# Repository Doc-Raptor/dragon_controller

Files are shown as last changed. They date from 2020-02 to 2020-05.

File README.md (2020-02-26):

This is a controller-board for 3d printers from china which are based on the anet printers and using an 8-bit board with 
on-board stepper driver and sometimes no fuse-protection (and no thermal-run-away).
This board is a low cost replacement with an stm32f103ret and socketed stepper drivers.
It is also capable of runnung from 24v.

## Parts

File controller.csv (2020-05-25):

ID | Bezeichner | Gehäuse | Stückzahl | Bezeichnung | Anbieter und Referenz
1 | J10 | PhoenixContact_GMSTBVA_2,5_2-G-7,62_1x02_P7.62mm_Vertical | 1 | Power_Heat
2 | J3 | PhoenixContact_GMSTBVA_2,5_2-G-7,62_1x02_P7.62mm_Vertical | 1 | Power_IN
3 | J1 | PinHeader_1x03_P2.54mm_Vertical | 1 | SPI
4 | U2 | LQFP-64_10x10mm_P0.5mm | 1 | STM32F103RETx
5 | Y1 | Crystal_SMD_5032-2Pin_5.0x3.2mm | 1 | Crystal
6 | R22,R21,R18,R12 | R_1206_3216Metric | 4 | 4K7
7 | R17,R11 | R_1206_3216Metric | 2 | 100
8 | R3,R7 | R_1206_3216Metric | 2 | 10K
9 | R2 | R_1206_3216Metric | 1 | 1K
10 | Q3 | TO-263-3_TabPin2 | 1 | HUF76639S3ST
11 | Q2 | SOT-23 | 1 | PMV40UN2
12 | Q1 | TO-263-3_TabPin2 | 1 | HY4903B
13 | J60 | PinHeader_1x04_P2.54mm_Vertical | 1 | e0-Stepper
14 | J52 | PinHeader_2x03_P2.54mm_Vertical | 1 | J_Y
15 | J51 | PinHeader_2x03_P2.54mm_Vertical | 1 | J_X
16 | J50 | PinHeader_2x03_P2.54mm_Vertical | 1 | J_E0
17 | J49 | PinHeader_2x03_P2.54mm_Vertical | 1 | J_Z
18 | J46 | PinHeader_1x02_P2.54mm_Vertical | 1 | 3.3V
19 | J45 | PinHeader_1x02_P2.54mm_Vertical | 1 | 5V
20 | J44,J9 | PinHeader_1x04_P2.54mm_Vertical | 2 | z-Stepper
21 | J43 | PinHeader_1x02_P2.54mm_Vertical | 1 | VCC
22 | J39 | PinHeader_1x04_P2.54mm_Vertical | 1 | y-Stepper
23 | J33 | PinHeader_1x04_P2.54mm_Vertical | 1 | x-Stepper
24 | J31 | PinHeader_1x04_P2.54mm_Vertical | 1 | Serial
25 | J30 | PinHeader_2x05_P2.54mm_Vertical | 1 | EXP2
26 | J29 | PinHeader_2x05_P2.54mm_Vertical | 1 | EXP1
27 | J28 | PinHeader_1x07_P2.54mm_Vertical | 1 | SD_CARD
28 | J17 | PinHeader_1x03_P2.54mm_Vertical | 1 | X-
29 | J16 | PinHeader_1x03_P2.54mm_Vertical | 1 | MAX_END
30 | J15 | PinHeader_1x03_P2.54mm_Vertical | 1 | Y-
31 | J14 | PinHeader_1x03_P2.54mm_Vertical | 1 | EXP3
32 | J13 | PinHeader_1x03_P2.54mm_Vertical | 1 | Z-
33 | J12 | PinHeader_1x03_P2.54mm_Vertical | 1 | BOOT
34 | J8 | PinHeader_1x02_P2.54mm_Vertical | 1 | Fan_Cooler
35 | J7 | PinHeader_1x03_P2.54mm_Vertical | 1 | SV1
36 | J6 | PinHeader_1x03_P2.54mm_Vertical | 1 | TH_B
37 | J5 | PhoenixContact_MCV_1,5_2-G-5.08_1x02_P5.08mm_Vertical | 1 | Hotend
38 | J2 | PinHeader_1x03_P2.54mm_Vertical | 1 | TH_E
39 | F2 | Fuseholder_Blade_ATO_Littelfuse_Pudenz_2_Pin | 1 | F_Heatbed_15A
40 | F1 | Fuseholder_Blade_ATO_Littelfuse_Pudenz_2_Pin | 1 | Fuse_Power
41 | D11,D8,D2 | D_SOD-123 | 3 | 1N5819
42 | C26,C24,C22,C20 | CP_Elec_6.3x7.7 | 4 | 100uF
43 | C18,C13,C10,C9,C8,C7,C6,C1 | C_1206_3216Metric | 8 | 100nF
44 | C17,C14 | C_0603_1608Metric | 2 | 20pF
45 | C16,C15,C11,C19 | C_1206_3216Metric | 4 | 10uF
46 | C12,C3,C4 | C_0805_2012Metric | 3 | 1uF
47 | A4,A3,A2,A1 | Pololu_Breakout-16_15.2x20.3mm | 4 | Pololu_Breakout_A4988
48 | H1,H2,H3,H4 | MountingHole_3.2mm_M3 | 4 | MountingHole
49 | SW1 | SW_Push_SPST_NO_Alps_SKRK | 1 | SW_Push
50 | C2 | C_1206_3216Metric | 1 | 4.7uF
51 | C5 | C_0603_1608Metric | 1 | 33pF
52 | D1 | D_SMA | 1 | B140-13-F
53 | L1 | L_1812_4532Metric | 1 | 4.7uH
54 | R1 | R_1206_3216Metric | 1 | 124K
55 | R4 | R_1206_3216Metric | 1 | 23K7
56 | U1 | SOT-23-6 | 1 | MP2451
57 | U3 | SOT-23-5 | 1 | RT9013-33GB
58 | R5 | R_1206_3216Metric | 1 | 100K

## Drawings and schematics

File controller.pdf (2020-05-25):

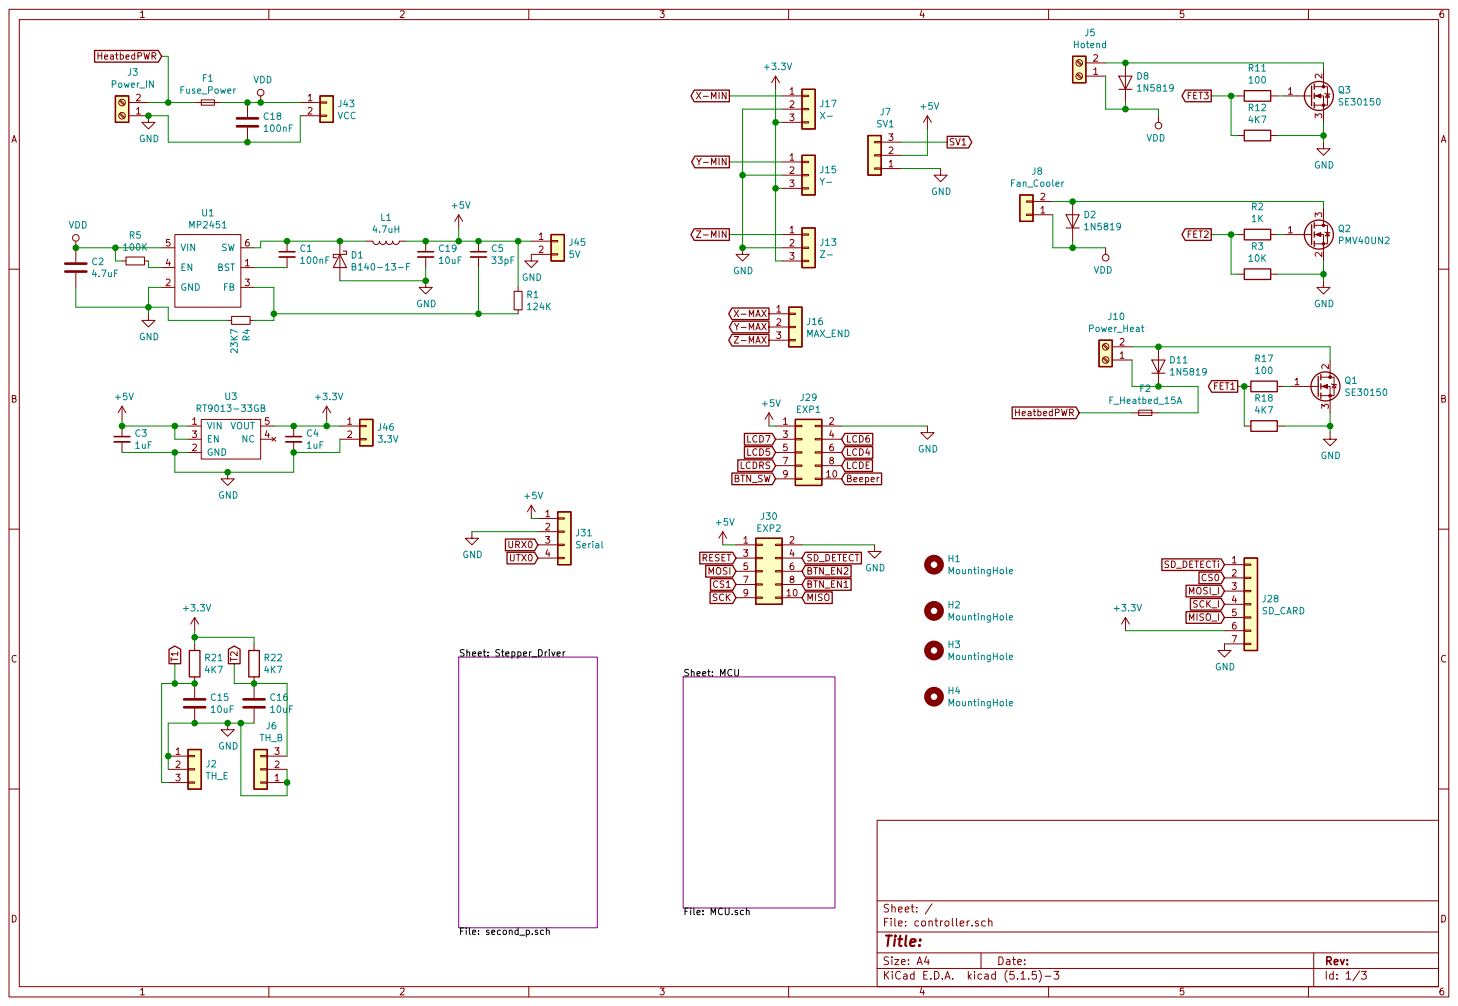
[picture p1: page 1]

Id: 1/3 Title: File: controller.sch Sheet: / Sheet: Stepper_Driver

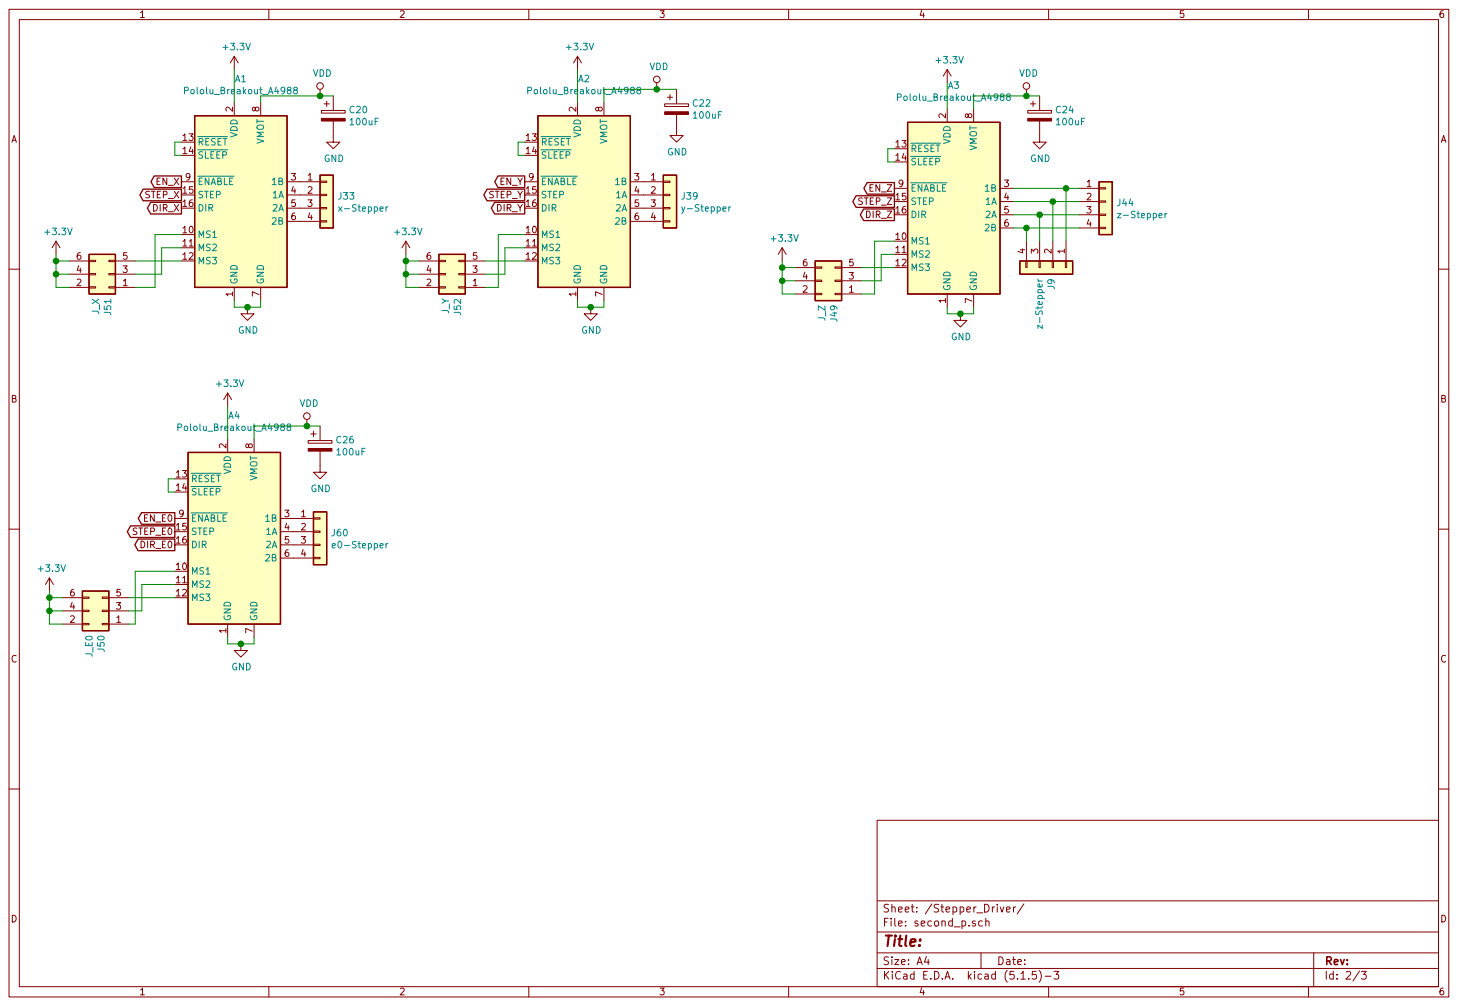
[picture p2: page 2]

8 ENABLE 9 A3 Pololu_Breakout_A4988 VDD GND GND GND

1 MS1 10 MS2 11 MS3 12 RESET 13 SLEEP 14 STEP 15 DIR 16 VDD

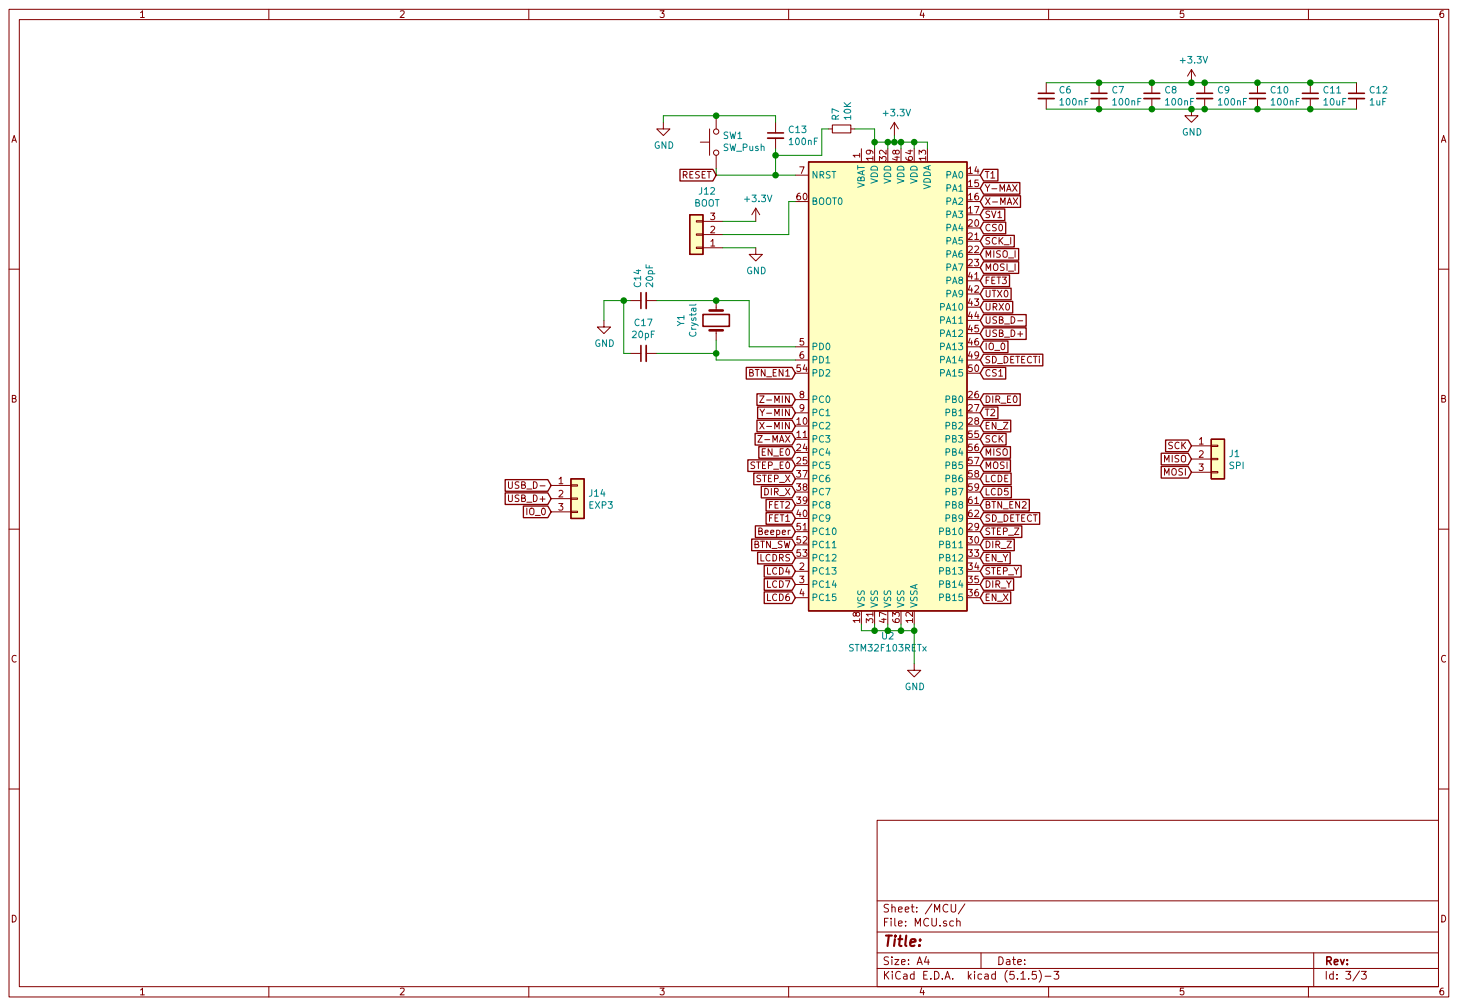
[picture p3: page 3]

Id: 3/3 Title: File: MCU.sch Sheet: /MCU/

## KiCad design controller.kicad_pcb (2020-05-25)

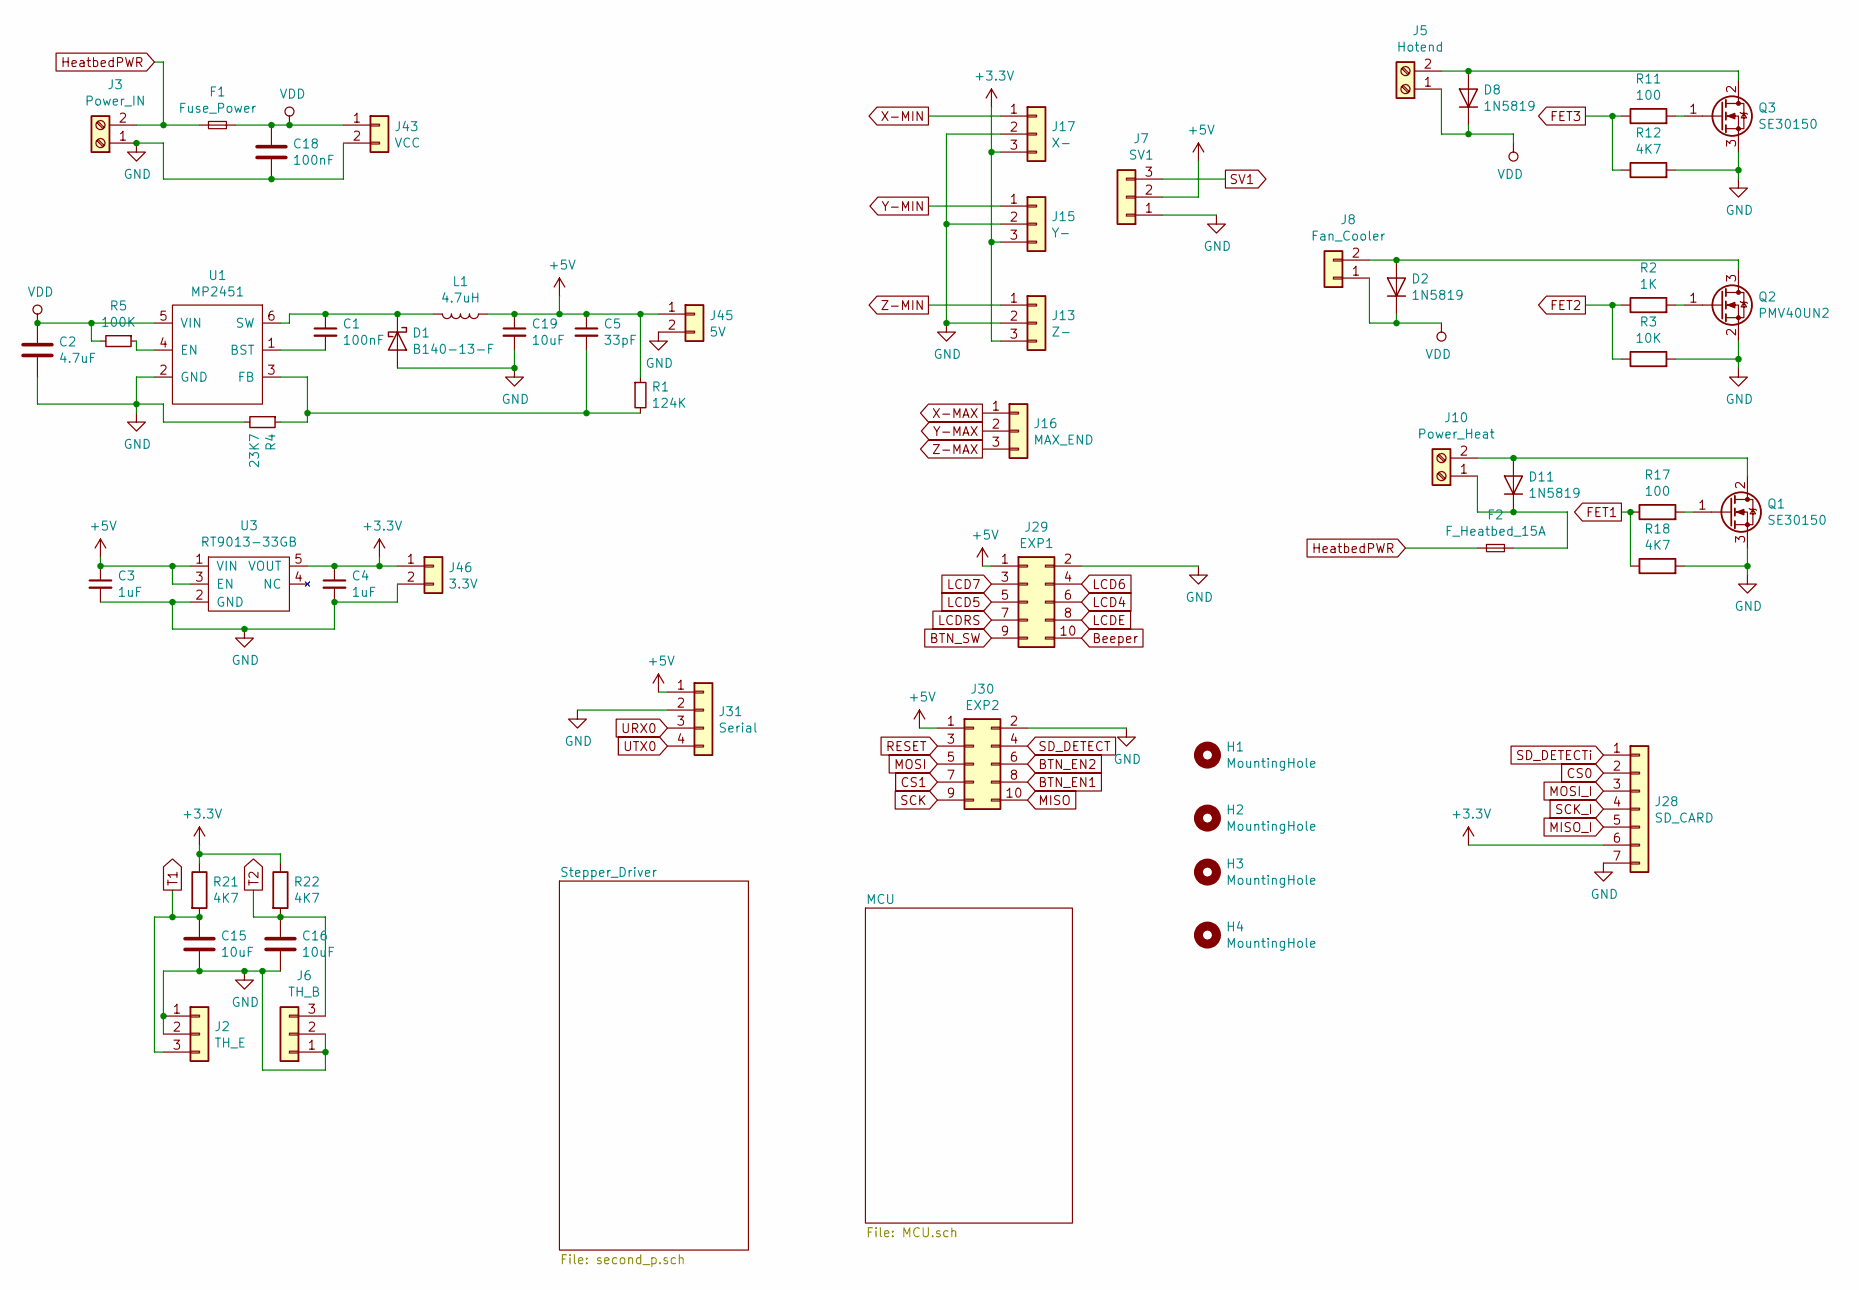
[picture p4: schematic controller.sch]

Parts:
C1, C18: 100nF; C_1206_3216Metric
C2: 4.7uF; C_1206_3216Metric
C3, C4: 1uF; C_0805_2012Metric
C5: 33pF; C_0603_1608Metric
C15, C16, C19: 10uF; C_1206_3216Metric
D1: B140-13-F; D_SMA
D2, D8, D11: 1N5819; D_SOD-123
F1: Fuse_Power; Fuseholder_Blade_ATO_Littelfuse_Pudenz_2_Pin
F2: F_Heatbed_15A; Fuseholder_Blade_ATO_Littelfuse_Pudenz_2_Pin
H1, H2, H3, H4: MountingHole; MountingHole_3.2mm_M3
J2: TH_E; PinHeader_1x03_P2.54mm_Vertical
J3: Power_IN; PhoenixContact_GMSTBVA_2,5_2-G-7,62_1x02_P7.62mm_Vertical
J5: Hotend; PhoenixContact_MCV_1,5_2-G-5.08_1x02_P5.08mm_Vertical
J6: TH_B; PinHeader_1x03_P2.54mm_Vertical
J7: SV1; PinHeader_1x03_P2.54mm_Vertical
J8: Fan_Cooler; PinHeader_1x02_P2.54mm_Vertical
J10: Power_Heat; PhoenixContact_GMSTBVA_2,5_2-G-7,62_1x02_P7.62mm_Vertical
J13: Z-; PinHeader_1x03_P2.54mm_Vertical
J15: Y-; PinHeader_1x03_P2.54mm_Vertical
J16: MAX_END; PinHeader_1x03_P2.54mm_Vertical
J17: X-; PinHeader_1x03_P2.54mm_Vertical
J28: SD_CARD; PinHeader_1x07_P2.54mm_Vertical
J29: EXP1; PinHeader_2x05_P2.54mm_Vertical
J30: EXP2; PinHeader_2x05_P2.54mm_Vertical
J31: Serial; PinHeader_1x04_P2.54mm_Vertical
J43: VCC; PinHeader_1x02_P2.54mm_Vertical
J45: 5V; PinHeader_1x02_P2.54mm_Vertical
J46: 3.3V; PinHeader_1x02_P2.54mm_Vertical
L1: 4.7uH; L_1812_4532Metric
Q1, Q3: SE30150; TO-263-3_TabPin2
Q2: PMV40UN2; SOT-23
R1: 124K; R_1206_3216Metric
R2: 1K; R_1206_3216Metric
R3: 10K; R_1206_3216Metric
R4: 23K7; R_1206_3216Metric
R5: 100K; R_1206_3216Metric
R11, R17: 100; R_1206_3216Metric
R12, R18, R21, R22: 4K7; R_1206_3216Metric
U1: MP2451; SOT-23-6
U3: RT9013-33GB; SOT-23-5

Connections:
+3V3: C4.1, J13.3, J15.3, J17.3, J28.6, J46.1, R21.1, R22.1, U3.5 (VOUT); also elsewhere on the board
+5V: C3.1, C5.1, C19.1, J7.2, J29.1, J30.1, J31.1, J45.1, L1.1, R1.1, U3.1 (VIN), U3.3 (EN)
BTN_EN1: J30.8; also elsewhere on the board
BTN_EN2: J30.6; also elsewhere on the board
BTN_SW: J29.9; also elsewhere on the board
Beeper: J29.10; also elsewhere on the board
CS0: J28.2; also elsewhere on the board
CS1: J30.7; also elsewhere on the board
FET1: R17.1, R18.1; also elsewhere on the board
FET2: R2.1, R3.1; also elsewhere on the board
FET3: R11.1, R12.1; also elsewhere on the board
GND: C2.2, C3.2, C4.2, C15.2, C16.2, C18.2, C19.2, D1.2 (A), J2.1, J2.2, J3.1, J6.1, J6.2, J7.1, J13.2, J15.2, J17.2, J28.7, J29.2, J30.2, J31.2, J43.2, J45.2, J46.2, Q1.3 (S), Q2.2 (S), Q3.3 (S), R3.2, R4.2, R12.2, R18.2, U1.2 (GND), U3.2 (GND); also elsewhere on the board
HeatbedPWR: F1.1, F2.1, J3.2
LCD4: J29.6; also elsewhere on the board
LCD5: J29.5; also elsewhere on the board
LCD6: J29.4; also elsewhere on the board
LCD7: J29.3; also elsewhere on the board
LCDE: J29.8; also elsewhere on the board
LCDRS: J29.7; also elsewhere on the board
MISO: J30.10; also elsewhere on the board
MISO_I: J28.5; also elsewhere on the board
MOSI: J30.5; also elsewhere on the board
MOSI_I: J28.3; also elsewhere on the board
unnamed: C1.1, D1.1 (K), L1.2, U1.6 (SW)
unnamed: C1.2, U1.1 (BST)
unnamed: C5.2, R1.2, R4.1, U1.3 (FB)
unnamed: D2.2 (A), J8.2, Q2.3 (D)
unnamed: D8.2 (A), J5.2, Q3.2 (D)
unnamed: D11.1 (K), F2.2, J10.1
unnamed: D11.2 (A), J10.2, Q1.2 (D)
unnamed: Q1.1 (G), R17.2
unnamed: Q2.1 (G), R2.2
unnamed: Q3.1 (G), R11.2
unnamed: R5.1, U1.4 (EN)
RESET: J30.3; also elsewhere on the board
SCK: J30.9; also elsewhere on the board
SCK_I: J28.4; also elsewhere on the board
SD_DETECT: J30.4; also elsewhere on the board
SD_DETECTi: J28.1; also elsewhere on the board
SV1: J7.3; also elsewhere on the board
T1: C15.1, J2.3, R21.2; also elsewhere on the board
T2: C16.1, J6.3, R22.2; also elsewhere on the board
URX0: J31.3; also elsewhere on the board
UTX0: J31.4; also elsewhere on the board
VDD: C2.1, C18.1, D2.1 (K), D8.1 (K), F1.2, J5.1, J8.1, J43.1, R5.2, U1.5 (VIN); also elsewhere on the board
X-MAX: J16.1; also elsewhere on the board
X-MIN: J17.1; also elsewhere on the board
Y-MAX: J16.2; also elsewhere on the board
Y-MIN: J15.1; also elsewhere on the board
Z-MAX: J16.3; also elsewhere on the board
Z-MIN: J13.1; also elsewhere on the board

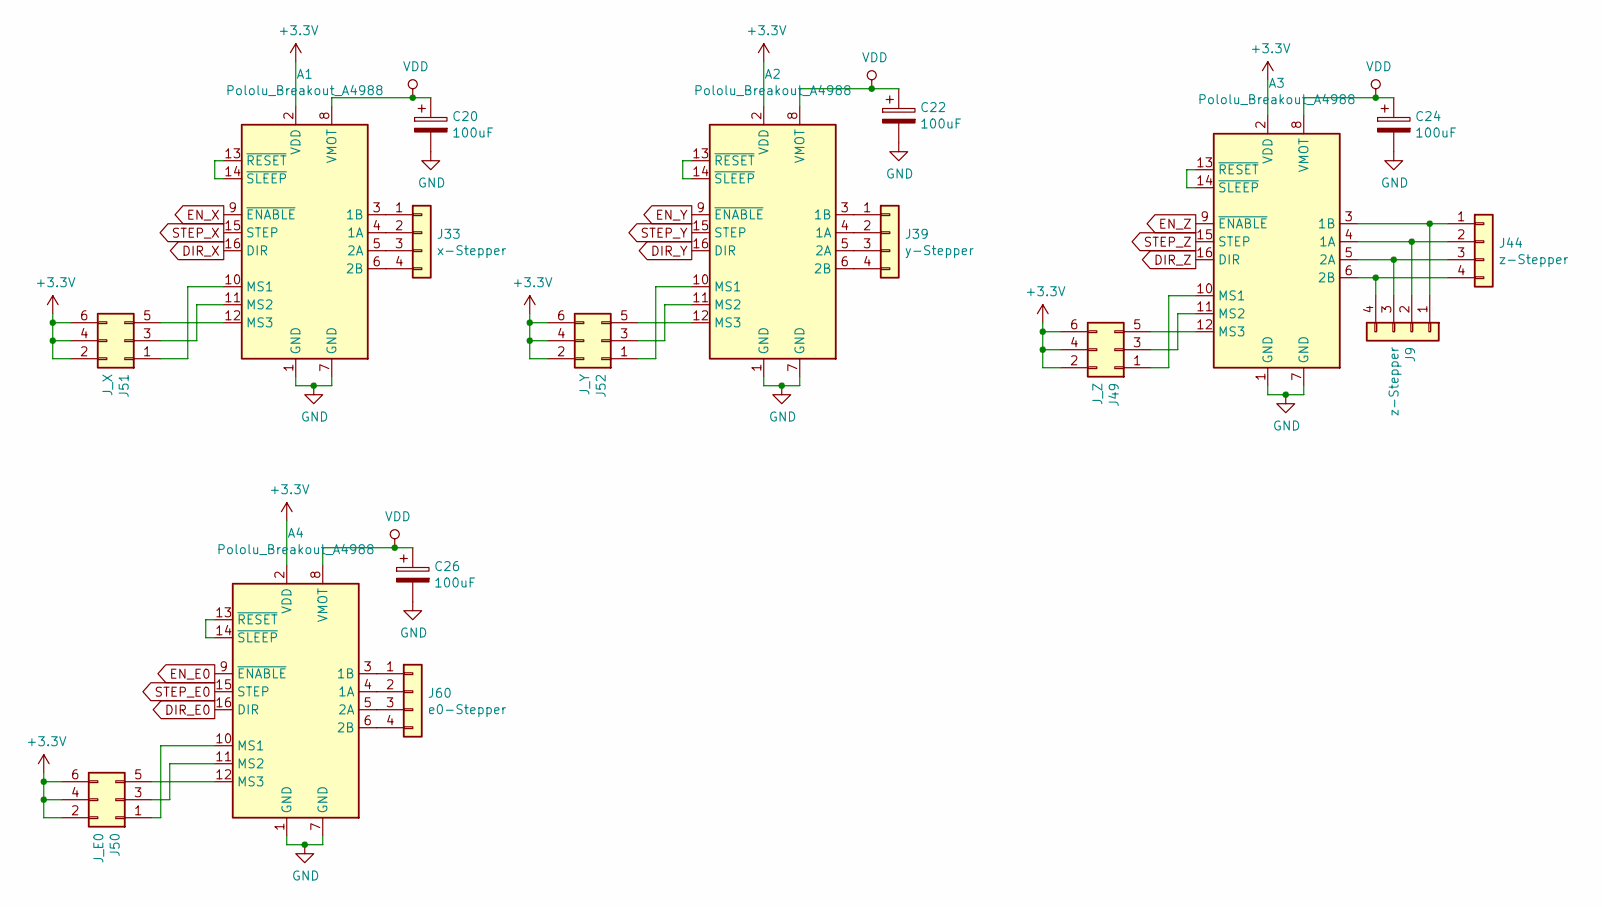
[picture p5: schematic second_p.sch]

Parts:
A1, A2, A3, A4: Pololu_Breakout_A4988; Pololu_Breakout-16_15.2x20.3mm
C20, C22, C24, C26: 100uF; CP_Elec_6.3x7.7
J9, J44: z-Stepper; PinHeader_1x04_P2.54mm_Vertical
J33: x-Stepper; PinHeader_1x04_P2.54mm_Vertical
J39: y-Stepper; PinHeader_1x04_P2.54mm_Vertical
J49: J_Z; PinHeader_2x03_P2.54mm_Vertical
J50: J_E0; PinHeader_2x03_P2.54mm_Vertical
J51: J_X; PinHeader_2x03_P2.54mm_Vertical
J52: J_Y; PinHeader_2x03_P2.54mm_Vertical
J60: e0-Stepper; PinHeader_1x04_P2.54mm_Vertical

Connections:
+3V3: A1.2 (VDD), A2.2 (VDD), A3.2 (VDD), A4.2 (VDD), J49.2, J49.4, J49.6, J50.2, J50.4, J50.6, J51.2, J51.4, J51.6, J52.2, J52.4, J52.6; also elsewhere on the board
DIR_E0: A4.16 (DIR); also elsewhere on the board
DIR_X: A1.16 (DIR); also elsewhere on the board
DIR_Y: A2.16 (DIR); also elsewhere on the board
DIR_Z: A3.16 (DIR); also elsewhere on the board
EN_E0: A4.9 (~ENABLE); also elsewhere on the board
EN_X: A1.9 (~ENABLE); also elsewhere on the board
EN_Y: A2.9 (~ENABLE); also elsewhere on the board
EN_Z: A3.9 (~ENABLE); also elsewhere on the board
GND: A1.1 (GND), A1.7 (GND), A2.1 (GND), A2.7 (GND), A3.1 (GND), A3.7 (GND), A4.1 (GND), A4.7 (GND), C20.2, C22.2, C24.2, C26.2; also elsewhere on the board
unnamed: A1.3 (1B), J33.1
unnamed: A1.4 (1A), J33.2
unnamed: A1.5 (2A), J33.3
unnamed: A1.6 (2B), J33.4
unnamed: A1.10 (MS1), J51.1
unnamed: A1.11 (MS2), J51.3
unnamed: A1.12 (MS3), J51.5
unnamed: A1.13 (~RESET), A1.14 (~SLEEP)
unnamed: A2.3 (1B), J39.1
unnamed: A2.4 (1A), J39.2
unnamed: A2.5 (2A), J39.3
unnamed: A2.6 (2B), J39.4
unnamed: A2.10 (MS1), J52.1
unnamed: A2.11 (MS2), J52.3
unnamed: A2.12 (MS3), J52.5
unnamed: A2.13 (~RESET), A2.14 (~SLEEP)
unnamed: A3.3 (1B), J9.1, J44.1
unnamed: A3.4 (1A), J9.2, J44.2
unnamed: A3.5 (2A), J9.3, J44.3
unnamed: A3.6 (2B), J9.4, J44.4
unnamed: A3.10 (MS1), J49.1
unnamed: A3.11 (MS2), J49.3
unnamed: A3.12 (MS3), J49.5
unnamed: A3.13 (~RESET), A3.14 (~SLEEP)
unnamed: A4.3 (1B), J60.1
unnamed: A4.4 (1A), J60.2
unnamed: A4.5 (2A), J60.3
unnamed: A4.6 (2B), J60.4
unnamed: A4.10 (MS1), J50.1
unnamed: A4.11 (MS2), J50.3
unnamed: A4.12 (MS3), J50.5
unnamed: A4.13 (~RESET), A4.14 (~SLEEP)
STEP_E0: A4.15 (STEP); also elsewhere on the board
STEP_X: A1.15 (STEP); also elsewhere on the board
STEP_Y: A2.15 (STEP); also elsewhere on the board
STEP_Z: A3.15 (STEP); also elsewhere on the board
VDD: A1.8 (VMOT), A2.8 (VMOT), A3.8 (VMOT), A4.8 (VMOT), C20.1, C22.1, C24.1, C26.1; also elsewhere on the board

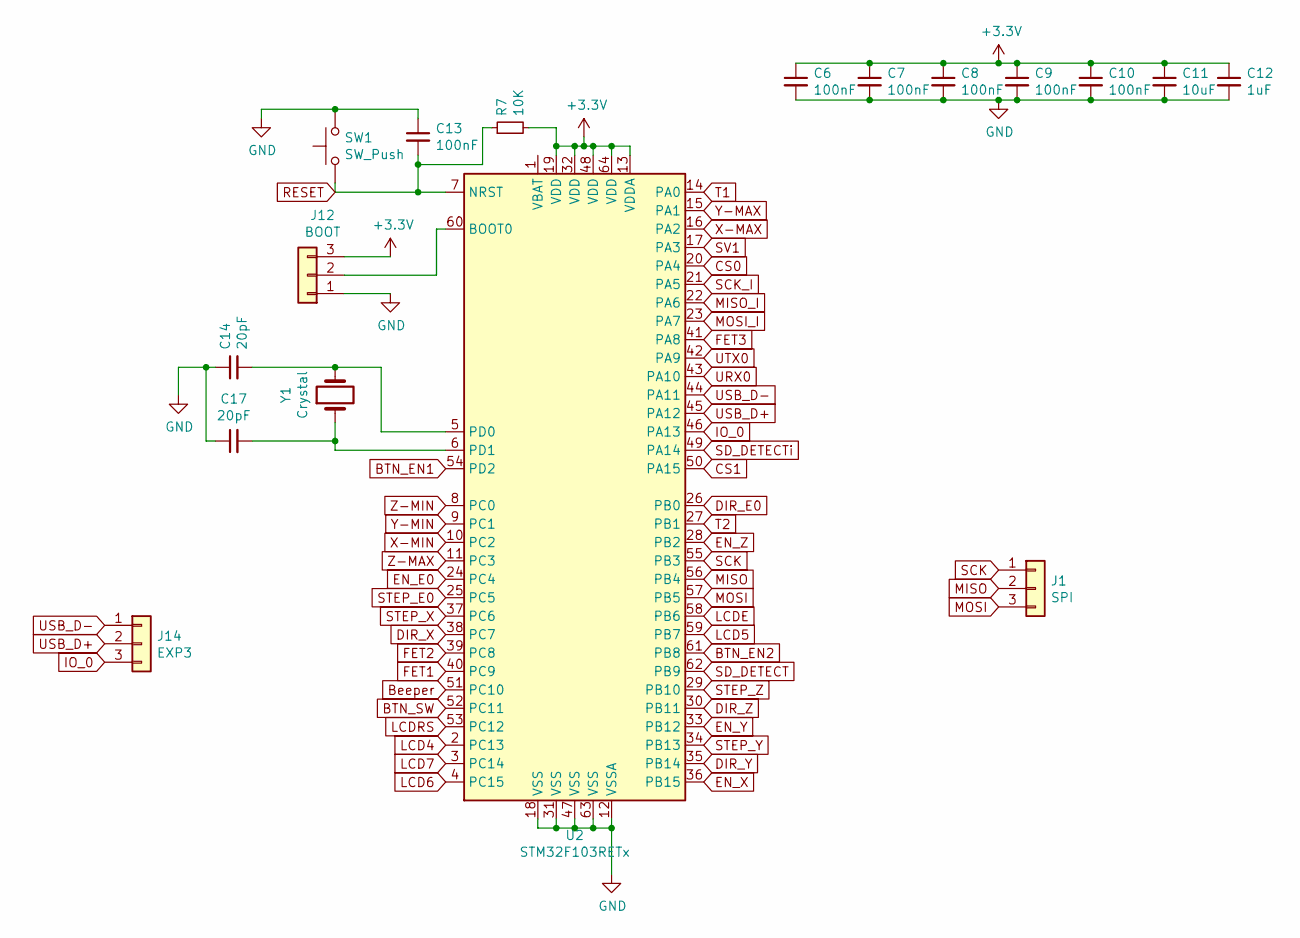
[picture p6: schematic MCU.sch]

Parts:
C6, C7, C8, C9, C10, C13: 100nF; C_1206_3216Metric
C11: 10uF; C_1206_3216Metric
C12: 1uF; C_0805_2012Metric
C14, C17: 20pF; C_0603_1608Metric
J1: SPI; PinHeader_1x03_P2.54mm_Vertical
J12: BOOT; PinHeader_1x03_P2.54mm_Vertical
J14: EXP3; PinHeader_1x03_P2.54mm_Vertical
R7: 10K; R_1206_3216Metric
SW1: SW_Push; SW_Push_SPST_NO_Alps_SKRK
U2: STM32F103RETx; LQFP-64_10x10mm_P0.5mm
Y1: Crystal; Crystal_SMD_5032-2Pin_5.0x3.2mm

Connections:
+3V3: C6.1, C7.1, C8.1, C9.1, C10.1, C11.1, C12.1, J12.3, R7.2, U2.13 (VDDA), U2.19 (VDD), U2.32 (VDD), U2.48 (VDD), U2.64 (VDD); also elsewhere on the board
BTN_EN1: U2.54 (PD2); also elsewhere on the board
BTN_EN2: U2.61 (PB8); also elsewhere on the board
BTN_SW: U2.52 (PC11); also elsewhere on the board
Beeper: U2.51 (PC10); also elsewhere on the board
CS0: U2.20 (PA4); also elsewhere on the board
CS1: U2.50 (PA15); also elsewhere on the board
DIR_E0: U2.26 (PB0); also elsewhere on the board
DIR_X: U2.38 (PC7); also elsewhere on the board
DIR_Y: U2.35 (PB14); also elsewhere on the board
DIR_Z: U2.30 (PB11); also elsewhere on the board
EN_E0: U2.24 (PC4); also elsewhere on the board
EN_X: U2.36 (PB15); also elsewhere on the board
EN_Y: U2.33 (PB12); also elsewhere on the board
EN_Z: U2.28 (PB2); also elsewhere on the board
FET1: U2.40 (PC9); also elsewhere on the board
FET2: U2.39 (PC8); also elsewhere on the board
FET3: U2.41 (PA8); also elsewhere on the board
GND: C6.2, C7.2, C8.2, C9.2, C10.2, C11.2, C12.2, C13.1, C14.1, C17.1, J12.1, SW1.2, U2.12 (VSSA), U2.18 (VSS), U2.31 (VSS), U2.47 (VSS), U2.63 (VSS); also elsewhere on the board
IO_0: J14.3, U2.46 (PA13)
LCD4: U2.2 (PC13); also elsewhere on the board
LCD5: U2.59 (PB7); also elsewhere on the board
LCD6: U2.4 (PC15); also elsewhere on the board
LCD7: U2.3 (PC14); also elsewhere on the board
LCDE: U2.58 (PB6); also elsewhere on the board
LCDRS: U2.53 (PC12); also elsewhere on the board
MISO: J1.2, U2.56 (PB4); also elsewhere on the board
MISO_I: U2.22 (PA6); also elsewhere on the board
MOSI: J1.3, U2.57 (PB5); also elsewhere on the board
MOSI_I: U2.23 (PA7); also elsewhere on the board
unnamed: C14.2, U2.5 (PD0), Y1.2
unnamed: C17.2, U2.6 (PD1), Y1.1
unnamed: J12.2, U2.60 (BOOT0)
RESET: C13.2, R7.1, SW1.1, U2.7 (NRST); also elsewhere on the board
SCK: J1.1, U2.55 (PB3); also elsewhere on the board
SCK_I: U2.21 (PA5); also elsewhere on the board
SD_DETECT: U2.62 (PB9); also elsewhere on the board
SD_DETECTi: U2.49 (PA14); also elsewhere on the board
STEP_E0: U2.25 (PC5); also elsewhere on the board
STEP_X: U2.37 (PC6); also elsewhere on the board
STEP_Y: U2.34 (PB13); also elsewhere on the board
STEP_Z: U2.29 (PB10); also elsewhere on the board
SV1: U2.17 (PA3); also elsewhere on the board
T1: U2.14 (PA0); also elsewhere on the board
T2: U2.27 (PB1); also elsewhere on the board
URX0: U2.43 (PA10); also elsewhere on the board
USB_D+: J14.2, U2.45 (PA12)
USB_D-: J14.1, U2.44 (PA11)
UTX0: U2.42 (PA9); also elsewhere on the board
X-MAX: U2.16 (PA2); also elsewhere on the board
X-MIN: U2.10 (PC2); also elsewhere on the board
Y-MAX: U2.15 (PA1); also elsewhere on the board
Y-MIN: U2.9 (PC1); also elsewhere on the board
Z-MAX: U2.11 (PC3); also elsewhere on the board
Z-MIN: U2.8 (PC0); also elsewhere on the board

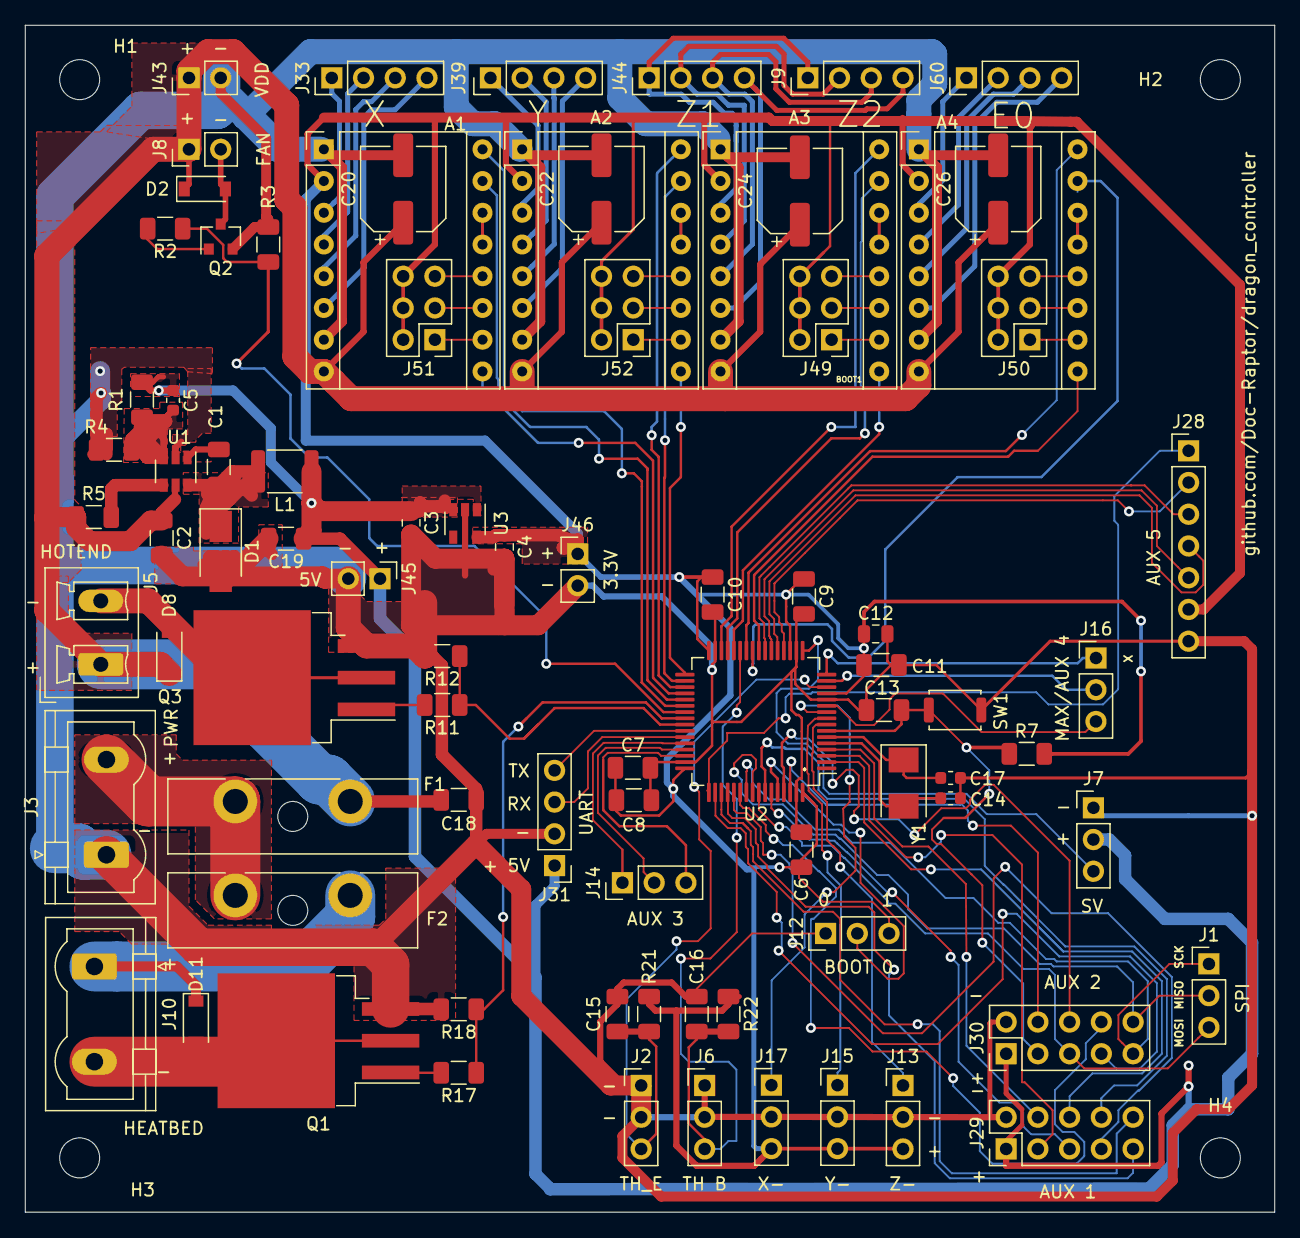
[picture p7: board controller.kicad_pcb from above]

Board: 2 copper layers, 100.0 x 95.0 mm, 88 parts (0 on the bottom side), 101 nets.

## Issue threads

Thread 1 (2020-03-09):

a bit of criticism.

r-pv, 2020-03-09:
Hi there, I'm thinking for a bit now to build an stm32 controller board too, so if you allow me to put my two cents on your board I think I can give you a little help.

So the first thing it's the mosfet you choose ( HUF76639S3ST ), didn't seems to be adequate for this task, their RDSON seems huge for the task, for the bed you should look for something below 10mΩ, the mosfet that you're using are 27mΩ at 10v, but you'll be using 3.3v for the gate so, if a read correctly the datasheet, you should be getting way higher RSDSON that the advertised 27mΩ and you'll get around 40mΩ, so if you are planing to use this at 24v on a typical 120w bed that'll be around 1W heat on the mosfet, you'll need active cooling (FAN)  and  for a 12v system that's 4W, I think this won't work for much. I'm planning to use the AON6522 or the AON7420, maybe a mix of both.

Next, the switching converter seems too old, you should look for a modern switching converter, after all, you won't be using more than 200mA for this. So for a 24v systems something like the MP1584 or the MP2451 are more than OK, for 12v you can use something like the MP2359.
In the same point, your layout for the switching converter are quite bad, on the datasheet of the IC that you'll be using check for the "layout recommendation" part and duplicate it, literately, big planes and component positions. If you are using a modern switching converter with a layout like you used on this controller it just won't work.

The tracks seems a bit thin, at least for the bed.

Cheers!.

Doc-Raptor, 2020-03-10:
Thanks for the Tips. I took the mosfet for the bed only for testing in the moment until I find something better. I only got the boards yesterday.
With the switching converter: It is not the newest and overkill, but literary every manufacturer has one in their lineup and it works even on a crued layout if it is under light load, but I will look in to the ones you recommended.
And I will increase the thickness of some of the tracks, when I finalize the layout and flood the pcb in some places with power and ground

Thanks and have a nice day

r-pv, 2020-03-11:
So I made a mistake, it's AON7520 (not 7420). If you like the THT mosfets the irlb8743 seems nice too, I'm using a controller with this mosfets and it's OK with 3v3 logic level. But if you can get a "gate driver" will be the best, but are a bit hard to get, at least to me.

Regarding the DC converter, you really should ditch it, not just because it's old, more because its working frequency, 52khz, it'll produce tons of EMI and probably will mess with the ADC readings if not with all, at very least you should add an RC filter after its output. The AMS1117, I used it and liked a lot but requires a lot of capacitance for working properly, I recently ditched it for the RT9013, all the new regulators are smaller, smarter, requires fewer capacitance/inductance and they just work better.

May I ask why you choose the F103RET MCU?, this part it's why I really decide anything, I what a simple controller without too much specs.

Cheers!.

Doc-Raptor, 2020-03-14:
I will be testing the HY4903B and SE30150. I bought them a few months ago most of them for someone else to safe shipping cost when I bought some PMV40UN2 and some other stuff. They have a RSDSON of 2mΩ when I looked it up two days ago. And they should drop in very easily.

The RT9013 sounds very good. When this board works I will replace the AMS1117 for the RT9013. Also the LM2575 could be replaced.

The F103RET (the f103 series in generaly) overing a lot for a relative low price. The F103RET should have enough memory for the firmware (if not the F103RF and F103RG should drop rigth in without problems). There are other factors, but overall the stm32f103 series overs for the price a lot.

r-pv, 2020-03-14:
The HY4903B sounds pretty good, at 3V3 seems that you'll get around 8mΩ, the SE30150 _seems_ better but the gate threshold it's at max 3v, too close to the 3V3 voltage, may not work, also, the datasheet didn't included an RDSOn graph to see how much resistance you can expect. Now, if you can get something that be a level shifter (PWM from 3v3 to 5v or 10v), that's another case!, ST has a [3printer board controller](https://www.st.com/en/evaluation-tools/steval-3dp001v1.html) that uses the SN74LVC1G125 as a level shifter, to get 5v PWM (or you can get a proper gate/mosfet driver). With an 5v PWM you will get an RDSOn of 2.1mΩ on the SE30150 and 3mΩ on the HY4903B.

The PMV40UN2 for switching FAN outputs seems pretty good, I'll use the AO34000A, but for this task there's not really any difference.

Cheers.

r-pv, 2020-03-18:
Hi, now it's looking great, just the layout requires a few details, check the datasheet of the IC: it says that you should put the components as close as possible (specially the capacitors), also, components like the mp2451 and modern switching regulators that work at high frequencies they need a big ground plane (you should use all available space on your pcb as ground plane, normally it's a good practice), I'll post how's the layout that I use and know that really works. The layout it's super important for this type of regulators, I remember that I used a layout like on your previous design for the MP1584, the regulator just give a random output from 50% to 95% of the VIN, it just won't work.

[rSTM32F103RCT6.pdf](https://github.com/Doc-Raptor/dragon_controller/files/4351832/rSTM32F103RCT6.pdf)

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

Closed 2020-03-14.

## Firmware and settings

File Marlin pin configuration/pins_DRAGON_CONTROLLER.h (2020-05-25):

/**
 * Marlin 3D Printer Firmware
 * Copyright (c) 2020 MarlinFirmware [https://github.com/MarlinFirmware/Marlin]
 *
 * Based on Sprinter and grbl.
 * Copyright (c) 2011 Camiel Gubbels / Erik van der Zalm
 *
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
 */
#pragma once

#ifndef __STM32F1__
  #error "Oops! Select an STM32F1 board in 'Tools > Board.'"
#endif

/**
 * 2020 DocRaptor
 */

#define BOARD_INFO_NAME      "Dragon Controller"
#define DEFAULT_MACHINE_NAME "32bit powered"

#define DISABLE_JTAG
// Ignore temp readings during development.
//#define BOGUS_TEMPERATURE_GRACE_PERIOD 2000
#define FLASH_EEPROM_EMULATION
#define EEPROM_PAGE_SIZE     (0x800) // 2KB
#define EEPROM_START_ADDRESS uint32(0x8000000 + (STM32_FLASH_SIZE) * 1024 - 2 * EEPROM_PAGE_SIZE)
#define E2END                (EEPROM_PAGE_SIZE - 1)

//
// Limit Switches
//
#define X_MIN_PIN                           PC2
#define X_MAX_PIN                           PA2
#define Y_MIN_PIN                           PC1
#define Y_MAX_PIN                           PA1
#define Z_MIN_PIN                           PC0
#define Z_MAX_PIN                           PC3

//
// Steppers
//

#define X_STEP_PIN                          PC6
#define X_DIR_PIN                           PC7
#define X_ENABLE_PIN                        PB15

#define Y_STEP_PIN                          PB13
#define Y_DIR_PIN                           PB14
#define Y_ENABLE_PIN                        PB12

#define Z_STEP_PIN                          PB10
#define Z_DIR_PIN                           PB11
#define Z_ENABLE_PIN                        PB2

#define E0_STEP_PIN                         PC5
#define E0_DIR_PIN                          PB0
#define E0_ENABLE_PIN                       PC4


//
// Servos
//
#define SERVO0_PIN                          PA3


//
// Heaters / Fans
//
#define HEATER_0_PIN                        PA8
#define FAN_PIN                             PC8
#define HEATER_BED_PIN                      PC9

//
// Temperature Sensors
//
#define TEMP_BED_PIN                        PB1   // Analog Input
#define TEMP_0_PIN                          PA0   // Analog Input

//
// LCD Pins
//

/**
 *                _____                                             _____
 *            5V | · · | GND                                    5V | · · | GND
 *         RESET | · · | PB9 (SD_DETECT)             (LCD_D7) PC14 | · · | PC15 (LCD_D6)
 *  (MOSI)   PB5 | · · | PB8 (BTN_EN2)               (LCD_D5)  PB7 | · · | PC13 (LCD_D4)
 * (SD_SS)  PA15 | · · | PD2 (BTN_EN1)               (LCD_RS) PC12 | · · | PB6  (LCD_EN)
 *   (SCK)   PB3 | · · | PB4 (MISO)                 (BTN_ENC) PC11 | · · | PC10 (BEEPER)
 *                -----                                             -----
 *                EXP2                                              EXP1
 */

#if HAS_SPI_LCD
  #define BEEPER_PIN                     PC10
  #define BTN_ENC                        PC11

  #if ENABLED(CR10_STOCKDISPLAY)
    #define LCD_PINS_RS                  PC15

    #define BTN_EN1                      PB6
    #define BTN_EN2                      PC13

    #define LCD_PINS_ENABLE              PC14
    #define LCD_PINS_D4                  PB7
	
	#define LCD_PINS_D5                  PB7
    #define LCD_PINS_D6                  PC15
    #define LCD_PINS_D7                  PC14

  #else

    #define LCD_PINS_RS                  PC12

    #define BTN_EN1                      PD2
    #define BTN_EN2                      PB8

    #define LCD_PINS_ENABLE              PB6

	
    #define LCD_PINS_D4                  PC13
    
	#define LCD_PINS_D5                  PB7
    #define LCD_PINS_D6                  PC15
    #define LCD_PINS_D7                  PC14


  #endif

#endif // HAS_SPI_LCD


//
// SD Card and SPI
//

#define ENABLE_SPI3
#define SD_DETECT_PIN                     PB9
#define SCK_PIN                           PB3
#define MISO_PIN                          PB4
#define MOSI_PIN                          PB5
#define SS_PIN                            PA15

#if HAS_GRAPHICAL_LCD
  #define BOARD_ST7920_DELAY_1 DELAY_NS(125)
  #define BOARD_ST7920_DELAY_2 DELAY_NS(125)
  #define BOARD_ST7920_DELAY_3 DELAY_NS(125)
#endif

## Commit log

2020-02-25 First Version
    Upload of the first version
    [MCU.sch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]
2020-02-27 Started to remove unneeded files
    [controller.kicad_pcb, controller.sch, second_p.sch]
2020-03-12 Modified power and ground at the Mosfets
    [MCU.sch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]
2020-03-18 New voltage regulators
    Replaced LM2575 with MP2451.
    Replaced AMS1117 with RT9013-33GB
    [controller-B_Cu.gbr, controller-B_Mask.gbr, controller-B_SilkS.gbr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]
2020-05-25 New Pinout and Marlin pin file
    Pinout, a marlin pin file and now being tested and most mistakes are corrected
    [MCU.sch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]

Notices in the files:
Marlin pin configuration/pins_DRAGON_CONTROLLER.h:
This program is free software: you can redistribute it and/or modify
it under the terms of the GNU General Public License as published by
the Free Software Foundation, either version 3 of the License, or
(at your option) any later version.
